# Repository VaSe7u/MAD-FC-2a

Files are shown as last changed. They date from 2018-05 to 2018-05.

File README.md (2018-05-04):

**MAD-FC-2a** quadrocopter flight controller.

This is a project of a flight controller for quadcopter. The [main source file][cpp] is designed to be descriptive of a multirotor flight controller algorithm. It is a concrete implementation that uses ATmega328P, MPU9255 and nRF24L01+ hardware but they can be easily replaced. The schematic and board layout for the flight controller and the remote board can be found in their respective circuit folders. The project depends on [MAD][madLink] library which is a common library for the flight controller and the remote.

*Not tested, Old project: [FC-alpha2][fcAlpha2].*

Flight Controller
=================
Schematic:
----------
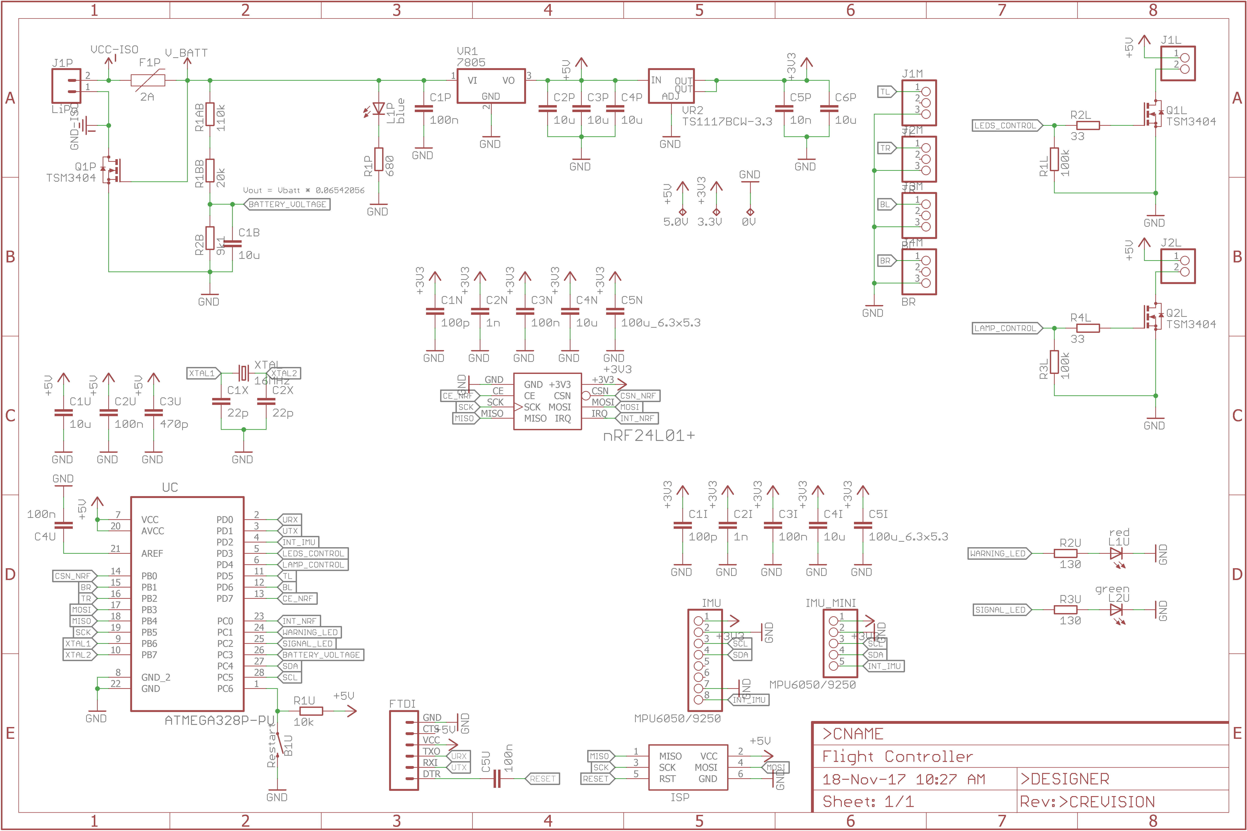
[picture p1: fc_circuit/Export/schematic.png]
sch


Board:
----------
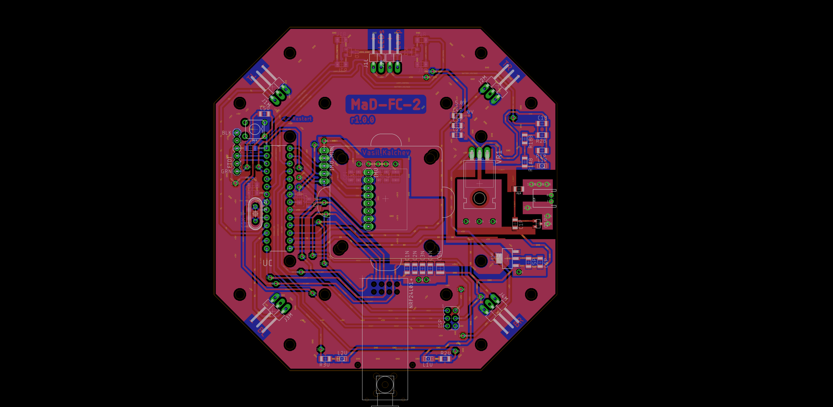
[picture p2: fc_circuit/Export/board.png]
brd

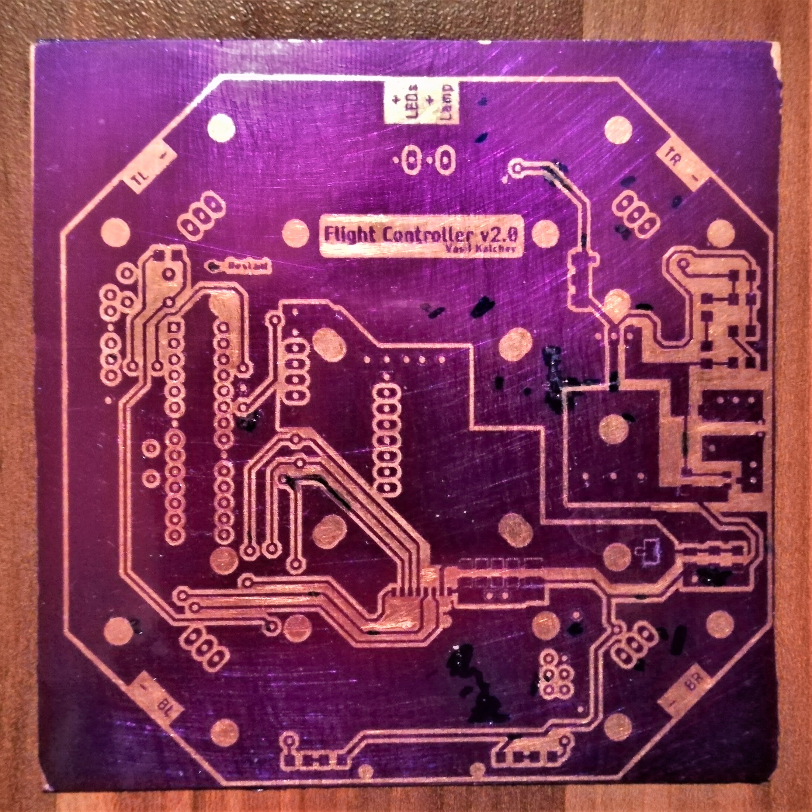
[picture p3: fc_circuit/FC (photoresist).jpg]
brdPhoto1

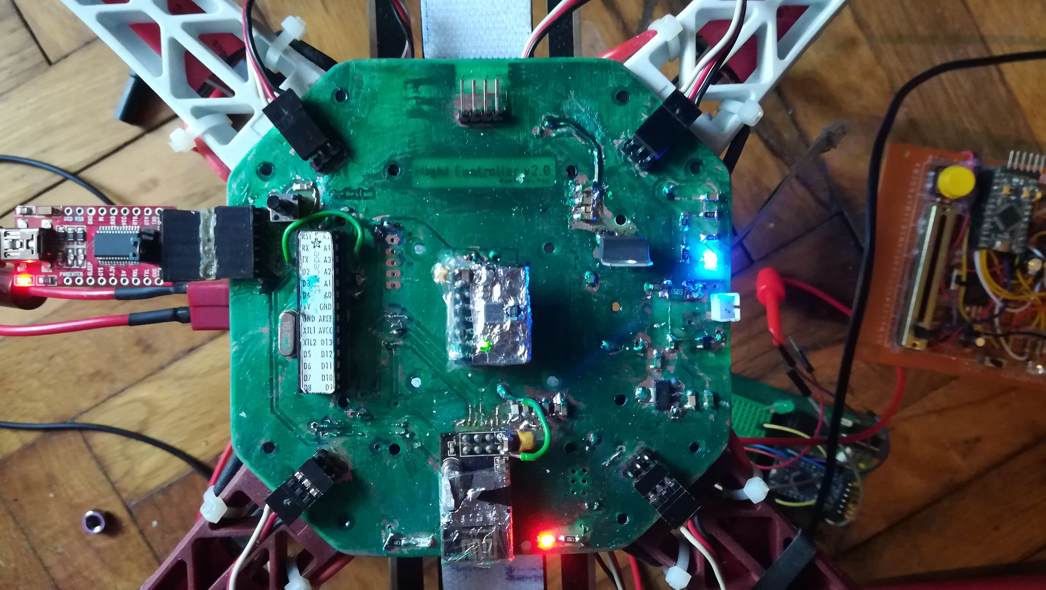
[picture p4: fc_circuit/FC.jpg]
brdPhoto2


Photo:
----------
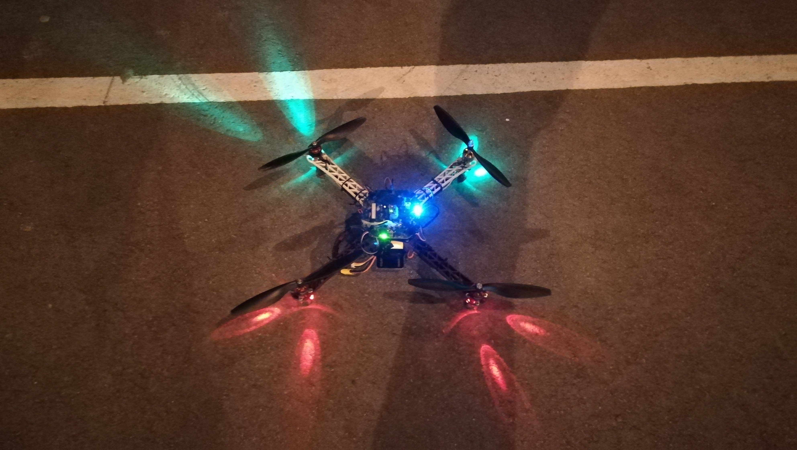
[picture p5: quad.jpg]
quadPhoto


Remote
======
Schematic:
----------
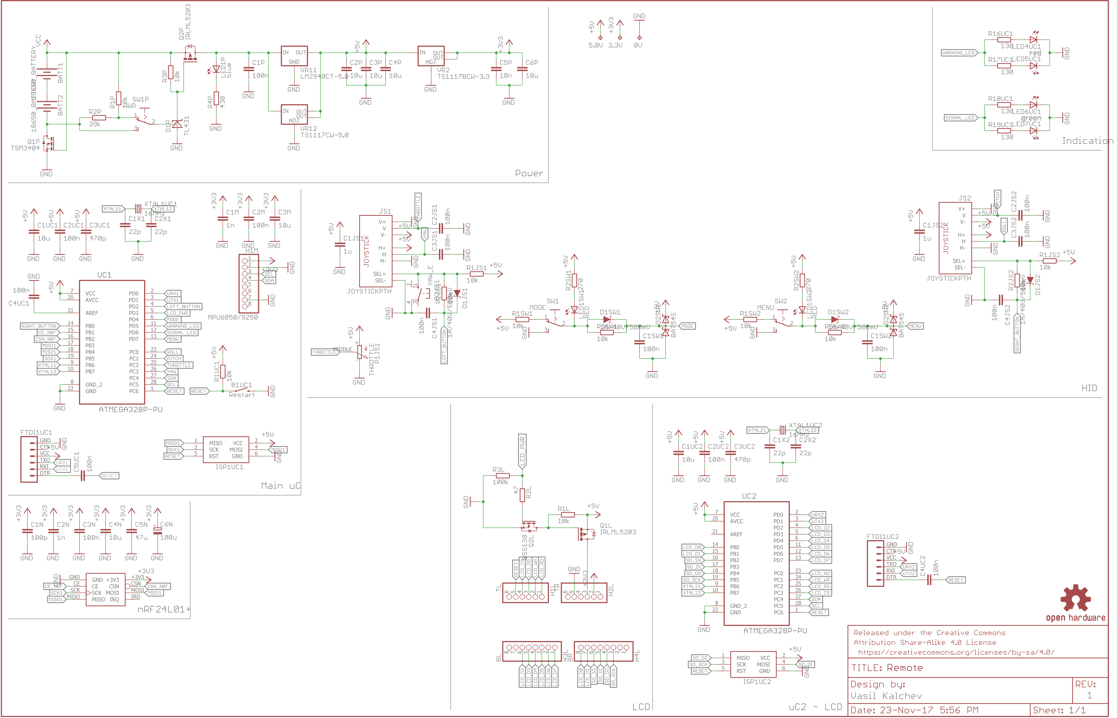
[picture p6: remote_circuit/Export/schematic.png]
rsch


Board:
----------
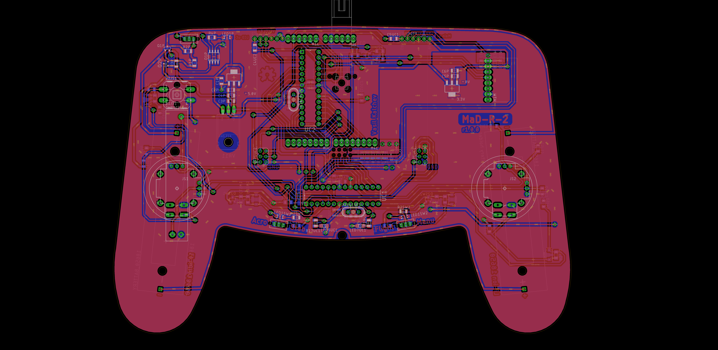
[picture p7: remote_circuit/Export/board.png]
rbrd


License
=======
The MIT License (MIT)

Copyright (c) 2016 Vasil Kalchev

Permission is hereby granted, free of charge, to any person obtaining a copy
of this software and associated documentation files (the "Software"), to deal
in the Software without restriction, including without limitation the rights
to use, copy, modify, merge, publish, distribute, sublicense, and/or sell
copies of the Software, and to permit persons to whom the Software is
furnished to do so, subject to the following conditions:

The above copyright notice and this permission notice shall be included in all
copies or substantial portions of the Software.

THE SOFTWARE IS PROVIDED "AS IS", WITHOUT WARRANTY OF ANY KIND, EXPRESS OR
IMPLIED, INCLUDING BUT NOT LIMITED TO THE WARRANTIES OF MERCHANTABILITY,
FITNESS FOR A PARTICULAR PURPOSE AND NONINFRINGEMENT. IN NO EVENT SHALL THE
AUTHORS OR COPYRIGHT HOLDERS BE LIABLE FOR ANY CLAIM, DAMAGES OR OTHER
LIABILITY, WHETHER IN AN ACTION OF CONTRACT, TORT OR OTHERWISE, ARISING FROM,
OUT OF OR IN CONNECTION WITH THE SOFTWARE OR THE USE OR OTHER DEALINGS IN THE
SOFTWARE.

[cpp]: https://github.com/VaSe7u/MAD-FC-2a/blob/master/code/MAD-FC-2a.ino
[madLink]: https://github.com/VaSe7u/MAD
[fcAlpha2]: https://github.com/VaSe7u/FC-alpha2

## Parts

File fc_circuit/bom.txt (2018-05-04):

Qty Value         Device                          Package
2   33            Resistor                        1206
2   130           Resistor                        1206
1   680           Resistor                        1206
1   9k1           Resistor                        1206
1   20k           Resistor                        1206
1   10k           Resistor                        1206
2   100k          Resistor                        1206
1   110k          Resistor                        1206

2   22p           Ceramic capacitor               1206
2   100p          Ceramic capacitor               1206
1   470p          Ceramic capacitor               1206
2   1n            Ceramic capacitor               1206
1   10n           Ceramic capacitor               1206
6   100n          Ceramic capacitor               1206
8   10u           Ceramic capacitor               1206

1   Conn          CONN_02JST-PTH-2                JST-2-PTH

1   SWITCH        MOMENTARY-SWITCH-SPST-PTH-6.0MM 6.0mm

1   blue          LED                             1206
1   green         LED                             1206
1   red           LED                             1206

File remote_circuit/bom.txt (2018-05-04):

Qty Value             Device                              Package
1   47                Resistor                            1206
4   130               Resistor                            1206
2   270               Resistor                            1206
1   430               Resistor                            1206
12  10k               Resistor                            1206
1   39k               Resistor                            1206
1   100k              Resistor                            1206

4   22p               Ceramic capacitor 16V               1206
1   100p              Ceramic capacitor 16V               1206
2   470p              Ceramic capacitor 16V               1206
2   1n                Ceramic capacitor 16V               1206
1   10n               Ceramic capacitor 16V               1206
16  100n              Ceramic capacitor 16V               1206
2   1u                Ceramic capacitor 16V               1206
8   10u               Ceramic capacitor 16V               1206
1   100u              Electrolytic capacitor 16V          6.3x5.3

1   TL431             TL431                               SO-8

1   BSS138            Transistor                          SOT23
2   IRLML5203         Transistor                          MICRO3

1   LM2940CT-5.0      Voltage regulator                   TO-220
1   TS1117CW-5.0      Voltage regulator                   SOT223
1   TS1117BCW-3.3     Voltage regulator                   SOT223

1   MOMENTARY-SWITCH  MOMENTARY-SWITCH-SPST-SMD           6x3,8mm

1   blue              LED                                 1206
2   green             LED                                 1206
4   red               LED                                 1206

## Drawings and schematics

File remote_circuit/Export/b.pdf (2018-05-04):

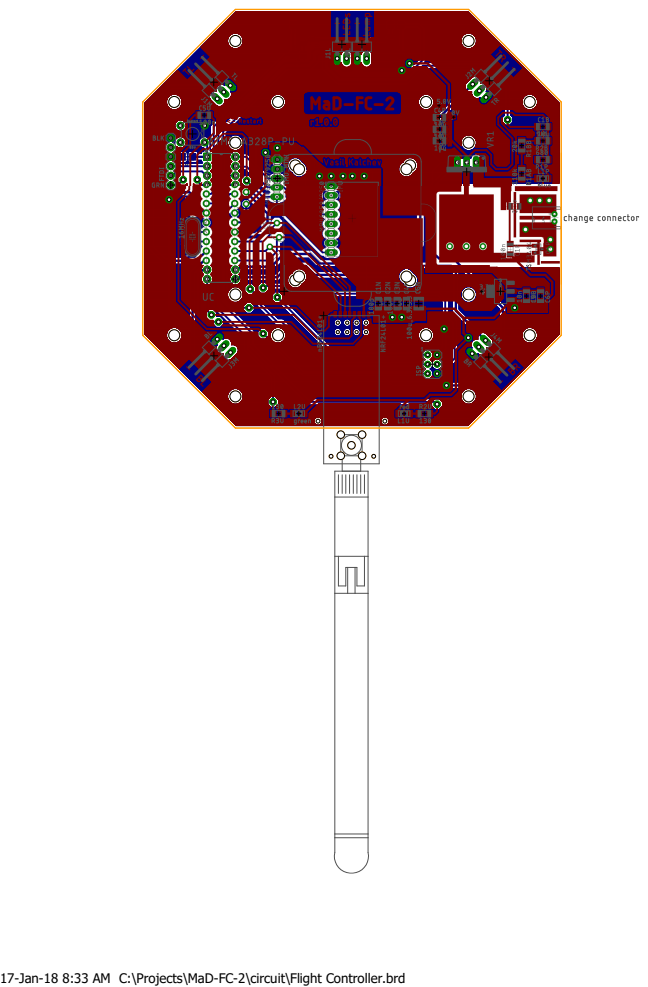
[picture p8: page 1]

17-Jan-18 8:33 AM C:\Projects\MaD-FC-2\circuit\Flight Controller.brd

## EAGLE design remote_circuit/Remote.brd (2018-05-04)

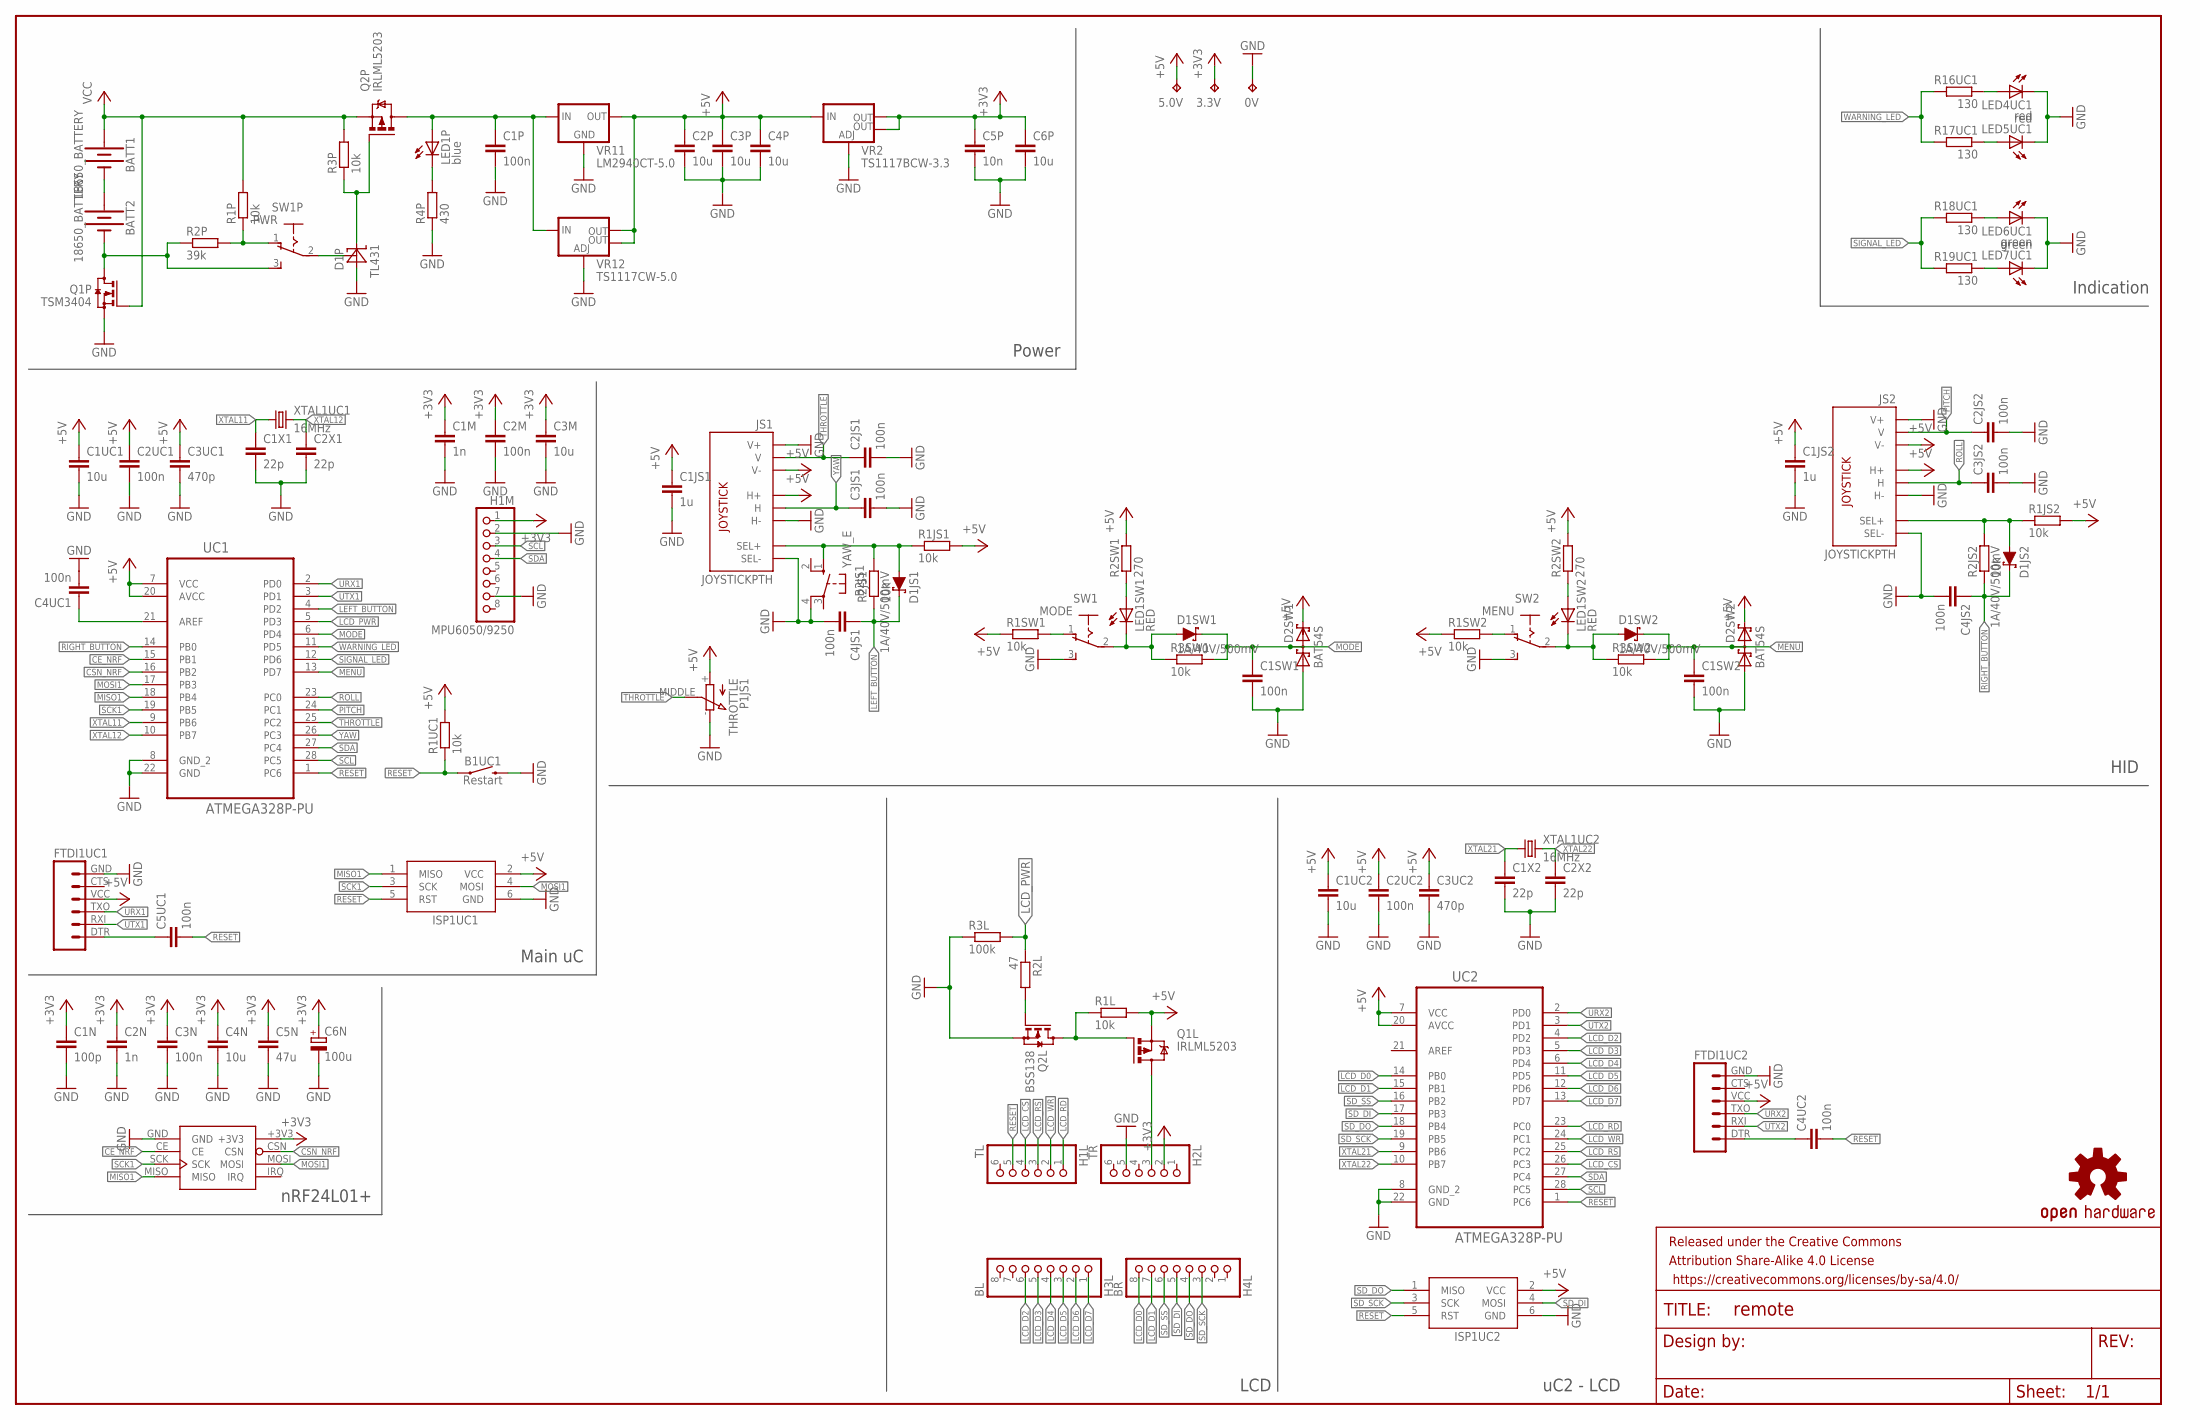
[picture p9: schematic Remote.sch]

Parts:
0V, 3.3V, 5.0V: TPTP10SQ; TP10SQ
B1: nRF24L01+; NRF24L01+_PA_LNA
B1UC1: Restart; TACTILE_SWITCH_SMD_6.0X3.5MM
B2JS1: YAW_E; B3F-40XX
BATT1, BATT2: 18650_BATTERY; BATTERY_HOLDER_18650
C1JS1, C1JS2: 1u; C1206
C1M, C2N: 1n; C1206
C1N: 100p; C1206
C1P, C1SW1, C1SW2, C2JS1, C2JS2, C2M, C2UC1, C2UC2, C3JS1, C3JS2, C3N, C4JS1, C4JS2, C4UC1, C4UC2, C5UC1: 100n; C1206
C1UC1, C1UC2, C2P, C3M, C3P, C4N, C4P, C6P: 10u; C1206
C1X1, C1X2, C2X1, C2X2: 22p; C1206
C3UC1, C3UC2: 470p; C1206
C5N: 47u; C3225
C5P: 10n; C1206
C6N: 100u; 153CLV-0505
D1JS1, D1JS2, D1SW1, D1SW2: 1A/40V/500mV; SMA-DIODE
D1P: TL431; SO-8
D2SW1, D2SW2: BAT54S; SOT23
FRAME2: FRAME-LEDGER; CREATIVE_COMMONS
FTDI1UC1, FTDI1UC2: FTDI_BASICPTH; FTDI_BASIC
H1L: TL; 1X06
H1M: MPU6050/9250; 1X08
H2L: TR; 1X06
H3L: BL; 1X08
H4L: BR; 1X08
ISP1UC1, ISP1UC2: AVRISP-6; AVRISP
JS1, JS2: JOYSTICKPTH; JOYSTICK
LED1P: blue; SML1206
LED1SW1, LED1SW2: RED; SML1206
LED4UC1: red; SML1206
LED5UC1: red; 1206
LED6UC1: green; SML1206
LED7UC1: green; 1206
LOGO1: OSHW-LOGOL-COPPER; OSHW-LOGO-L_COPPER
P1JS1: THROTTLE; SLIDE_POTENTIOMETER
Q1L, Q2P: IRLML5203; MICRO3
Q1P: TSM3404; SOT23
Q2L: BSS138; SOT23
R1JS1, R1JS2, R1L, R1P, R1SW1, R1SW2, R1UC1, R2JS1, R2JS2, R3P, R3SW1, R3SW2: 10k; R1206
R2L: 47; R1206
R2P: 39k; R1206
R2SW1, R2SW2: 270; R1206
R3L: 100k; R1206
R4P: 430; R1206
R16UC1, R17UC1, R18UC1, R19UC1: 130; R1206
SW1: MODE; SWITCH_2MM
SW1P: PWR; SWITCH_2MM
SW2: MENU; SWITCH_2MM
UC1, UC2: ATMEGA328P-PU; DIP254P762X457-28
VR2: TS1117BCW-3.3; SOT223
VR11: LM2940CT-5.0; 78XXL
VR12: TS1117CW-5.0; SOT223
XTAL1UC1, XTAL1UC2: 16MHz; HC49/S

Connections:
+3V3: 3.3V.TP, B1.+3V3, C1M.1, C1N.1, C2M.1, C2N.1, C3M.1, C3N.1, C4N.1, C5N.1, C5P.1, C6N.+, C6P.1, H1M.1, H2L.2, VR2.2 (OUT), VR2.4 (OUT)
+5V: 5.0V.TP, C1JS1.1, C1JS2.1, C1UC1.1, C1UC2.1, C2P.1, C2UC1.1, C2UC2.1, C3P.1, C3UC1.1, C3UC2.1, C4P.1, D2SW1.2 (C2), D2SW2.2 (C2), FTDI1UC1.VCC (4), FTDI1UC2.VCC (4), ISP1UC1.2 (VCC), ISP1UC2.2 (VCC), JS1.H1 (H+), JS1.V3 (V-), JS2.H1 (H+), JS2.V3 (V-), P1JS1.+, Q1L.2 (S), R1JS1.2, R1JS2.2, R1L.2, R1SW1.1, R1SW2.1, R1UC1.2, R2SW1.2, R2SW2.2, UC1.7 (VCC), UC1.20 (AVCC), UC2.7 (VCC), UC2.20 (AVCC), VR2.3 (IN), VR11.OUT, VR12.2 (OUT), VR12.4 (OUT)
CE_NRF: B1.CE, UC1.15 (PB1)
CSN_NRF: B1.CSN, UC1.16 (PB2)
GND: 0V.TP, B1.GND, B1UC1.2, B2JS1.4 (P1), C1JS1.2, C1JS2.2, C1M.2, C1N.2, C1P.2, C1SW1.2, C1SW2.2, C1UC1.2, C1UC2.2, C1X1.2, C1X2.2, C2JS1.2, C2JS2.2, C2M.2, C2N.2, C2P.2, C2UC1.2, C2UC2.2, C2X1.2, C2X2.2, C3JS1.2, C3JS2.2, C3M.2, C3N.2, C3P.2, C3UC1.2, C3UC2.2, C4JS1.2, C4JS2.2, C4N.2, C4P.2, C4UC1.2, C5N.2, C5P.2, C6N.-, C6P.2, D1P.2 (ANODE), D1P.3 (ANODE), D1P.6 (ANODE), D1P.7 (ANODE), D2SW1.1 (A1), D2SW2.1 (A1), FTDI1UC1.GND (6), FTDI1UC2.GND (6), H1M.2, H1M.7, H2L.5, ISP1UC1.6 (GND), ISP1UC2.6 (GND), JS1.B2A (SEL-), JS1.H3 (H-), JS1.V1 (V+), JS2.B2A (SEL-), JS2.H3 (H-), JS2.V1 (V+), LED4UC1.C, LED5UC1.C, LED6UC1.C, LED7UC1.C, P1JS1.-, Q1P.2 (S), Q2L.2 (S), R3L.1, R4P.1, SW1.3, SW2.3, UC1.8 (GND_2), UC1.22 (GND), UC2.8 (GND_2), UC2.22 (GND), VR2.1 (ADJ), VR11.GND, VR12.1 (ADJ)
LCD_CS: H1L.4, UC2.26 (PC3)
LCD_D0: H4L.8, UC2.14 (PB0)
LCD_D1: H4L.7, UC2.15 (PB1)
LCD_D2: H3L.6, UC2.4 (PD2)
LCD_D3: H3L.5, UC2.5 (PD3)
LCD_D4: H3L.4, UC2.6 (PD4)
LCD_D5: H3L.3, UC2.11 (PD5)
LCD_D6: H3L.2, UC2.12 (PD6)
LCD_D7: H3L.1, UC2.13 (PD7)
LCD_PWR: R2L.1, R3L.2, UC1.5 (PD3)
LCD_RD: H1L.1, UC2.23 (PC0)
LCD_RS: H1L.3, UC2.25 (PC2)
LCD_WR: H1L.2, UC2.24 (PC1)
LEFT_BUTTON: C4JS1.1, D1JS1.C, R2JS1.1, UC1.4 (PD2)
MENU: C1SW2.1, D1SW2.C, D2SW2.3 (C1A2), R3SW2.2, UC1.13 (PD7)
MISO1: B1.MISO, ISP1UC1.1 (MISO), UC1.18 (PB4)
MODE: C1SW1.1, D1SW1.C, D2SW1.3 (C1A2), R3SW1.2, UC1.6 (PD4)
MOSI1: B1.MOSI, ISP1UC1.4 (MOSI), UC1.17 (PB3)
unnamed: C4UC1.1, UC1.21 (AREF)
unnamed: LED1SW1.A, R2SW1.1
unnamed: C5UC1.1, FTDI1UC1.DTR (1)
unnamed: BATT1.-, BATT2.+
unnamed: R1SW2.2, SW2.1
unnamed: D1SW2.A, LED1SW2.C, R3SW2.1, SW2.2
unnamed: LED1P.C, R4P.2
unnamed: D1SW1.A, LED1SW1.C, R3SW1.1, SW1.2
unnamed: LED1SW2.A, R2SW2.1
unnamed: R1SW1.2, SW1.1
unnamed: D1JS2.A, JS2.B1A (SEL+), R1JS2.1, R2JS2.2
unnamed: BATT2.-, Q1P.3 (D), R2P.1, SW1P.3
unnamed: LED4UC1.A, R16UC1.1
unnamed: LED6UC1.A, R18UC1.1
unnamed: C4UC2.1, FTDI1UC2.DTR (1)
unnamed: LED5UC1.A, R17UC1.1
unnamed: H2L.3, Q1L.3 (D)
unnamed: LED7UC1.A, R19UC1.1
unnamed: C1P.1, LED1P.A, Q2P.3 (D), VR11.IN, VR12.3 (IN)
unnamed: D1P.8 (REFERENCE), SW1P.2
unnamed: R1P.1, R2P.2, SW1P.1
unnamed: Q1L.1 (G), Q2L.3 (D), R1L.1
unnamed: D1P.1 (CATHODE), Q2P.1 (G), R3P.1
unnamed: Q2L.1 (G), R2L.2
PITCH: C2JS2.1, JS2.V2 (V), UC1.24 (PC1)
RESET: B1UC1.1, C4UC2.2, C5UC1.2, H1L.5, ISP1UC1.5 (RST), ISP1UC2.5 (RST), R1UC1.1, UC1.1 (PC6), UC2.1 (PC6)
RIGHT_BUTTON: C4JS2.1, D1JS2.C, R2JS2.1, UC1.14 (PB0)
ROLL: C3JS2.1, JS2.H2 (H), UC1.23 (PC0)
SCK1: B1.SCK, ISP1UC1.3 (SCK), UC1.19 (PB5)
SCL: H1M.3, UC1.28 (PC5), UC2.28 (PC5)
SDA: H1M.4, UC1.27 (PC4), UC2.27 (PC4)
SD_DI: H4L.5, ISP1UC2.4 (MOSI), UC2.17 (PB3)
SD_DO: H4L.4, ISP1UC2.1 (MISO), UC2.18 (PB4)
SD_SCK: H4L.3, ISP1UC2.3 (SCK), UC2.19 (PB5)
SD_SS: H4L.6, UC2.16 (PB2)
SIGNAL_LED: R18UC1.2, R19UC1.2, UC1.12 (PD6)
SN1: B2JS1.1 (S), D1JS1.A, JS1.B1A (SEL+), R1JS1.1, R2JS1.2
THROTTLE: C2JS1.1, JS1.V2 (V), P1JS1.MIDDLE, UC1.25 (PC2)
URX1: FTDI1UC1.TXO (3), UC1.2 (PD0)
URX2: FTDI1UC2.TXO (3), UC2.2 (PD0)
UTX1: FTDI1UC1.RXI (2), UC1.3 (PD1)
UTX2: FTDI1UC2.RXI (2), UC2.3 (PD1)
VCC: BATT1.+, Q1P.1 (G), Q2P.2 (S), R1P.2, R3P.2
WARNING_LED: R16UC1.2, R17UC1.2, UC1.11 (PD5)
XTAL11: C1X1.1, UC1.9 (PB6), XTAL1UC1.1
XTAL12: C2X1.1, UC1.10 (PB7), XTAL1UC1.2
XTAL21: C1X2.1, UC2.9 (PB6), XTAL1UC2.1
XTAL22: C2X2.1, UC2.10 (PB7), XTAL1UC2.2
YAW: C3JS1.1, JS1.H2 (H), UC1.26 (PC3)

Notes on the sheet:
Power
nRF24L01+
LCD
uC2 - LCD
HID
Indication
Main uC

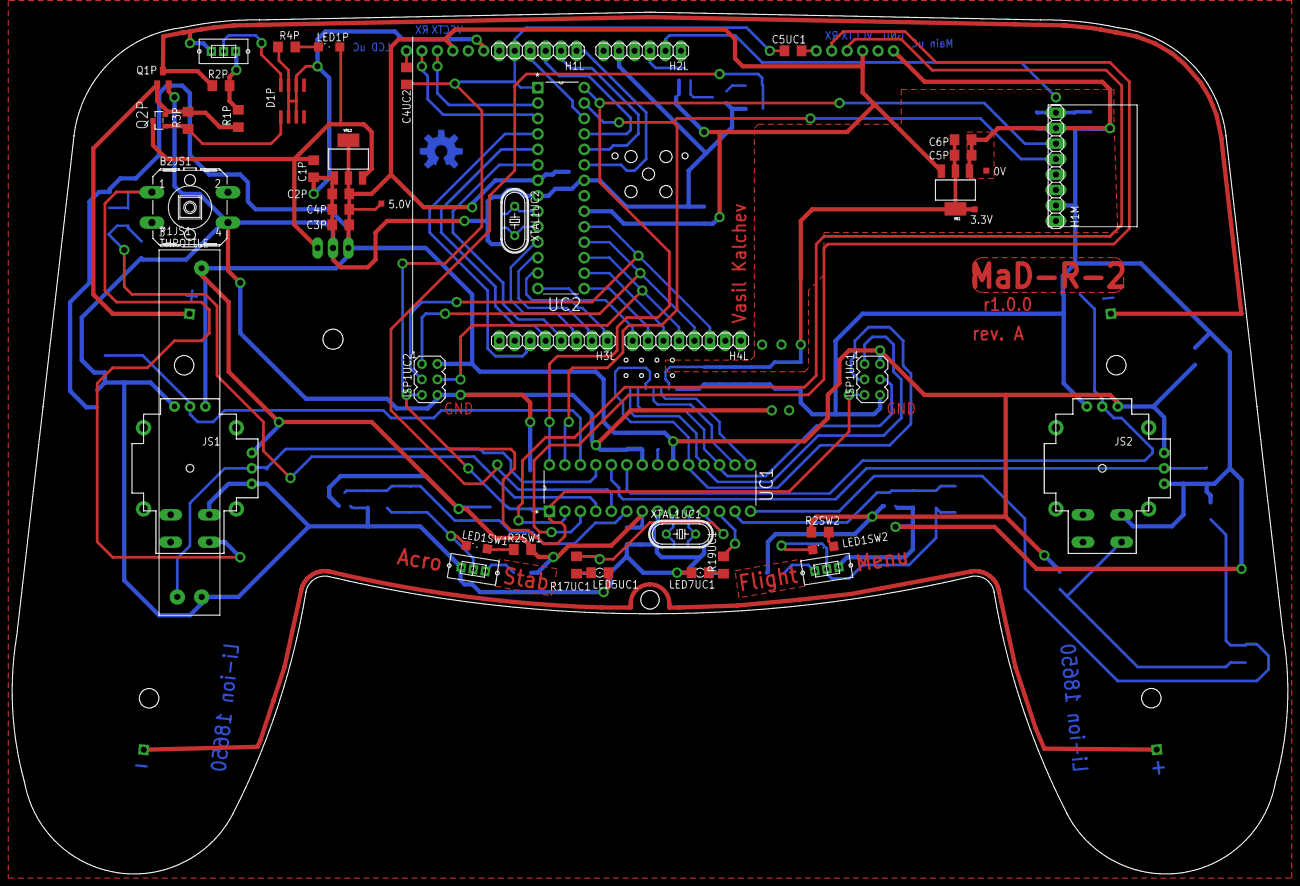
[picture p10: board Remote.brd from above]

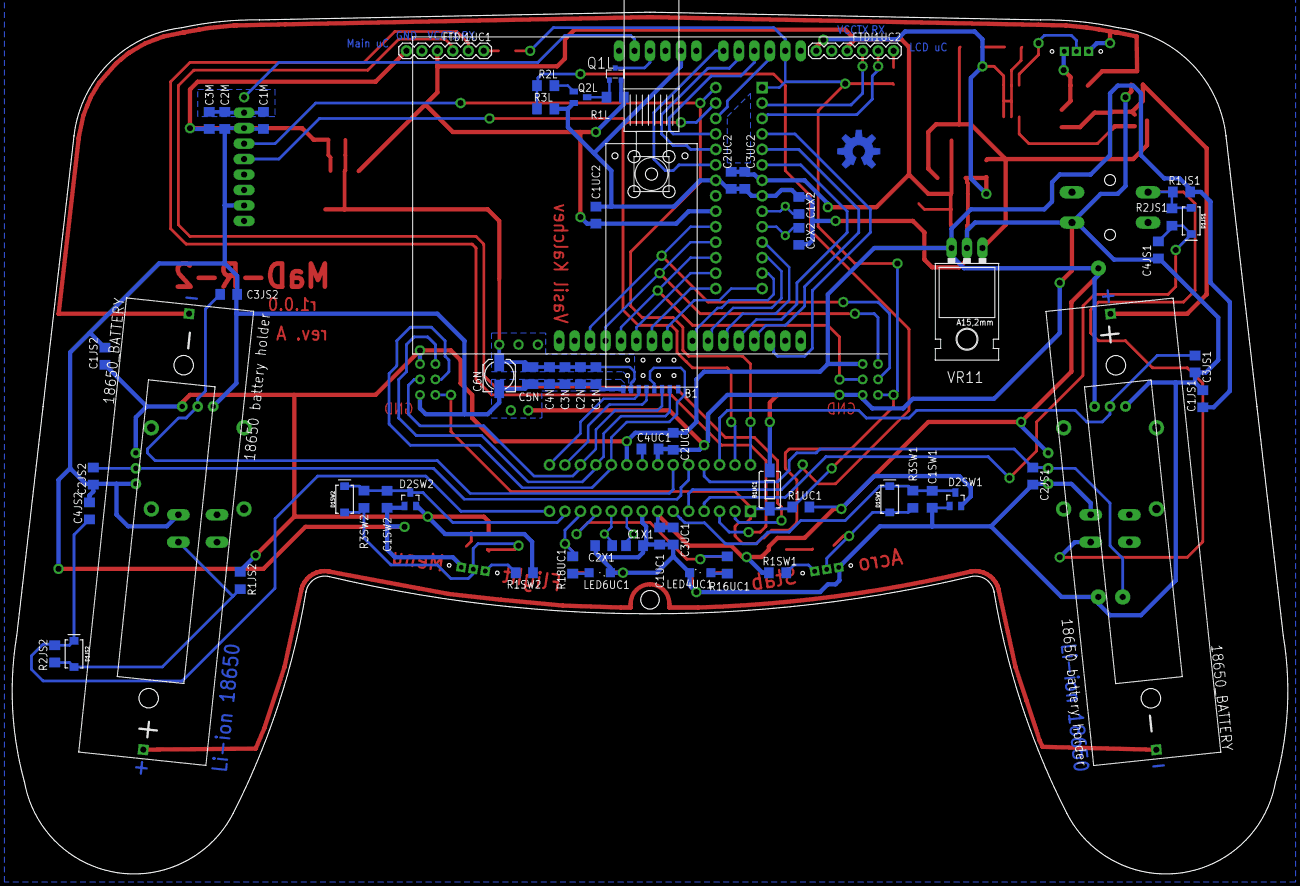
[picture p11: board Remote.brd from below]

Board: 2 copper layers, 209.5 x 141.5 mm, 110 parts (62 on the bottom side), 72 nets.

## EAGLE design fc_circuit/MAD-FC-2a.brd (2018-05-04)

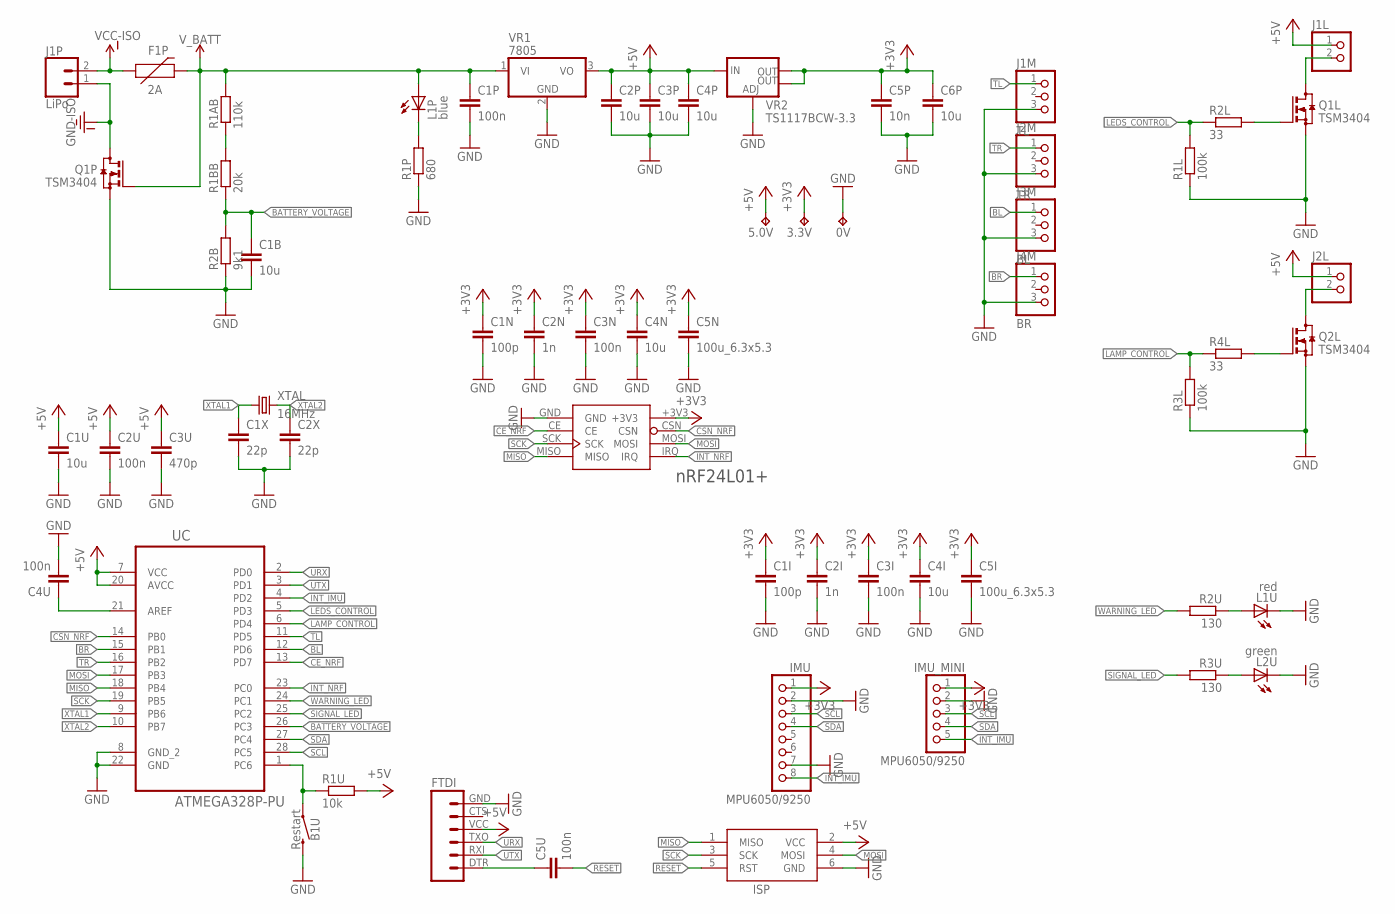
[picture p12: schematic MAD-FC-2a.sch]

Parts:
0V, 3.3V, 5.0V: TPTP10SQ; TP10SQ
B1U: Restart; TACTILE_SWITCH_PTH_6.0MM
C1B, C1U, C2P, C3P, C4I, C4N, C4P, C6P: 10u; C1206
C1I, C1N: 100p; C1206
C1P, C2U, C3I, C3N, C4U, C5U: 100n; C1206
C1X, C2X: 22p; C1206
C2I, C2N: 1n; C1206
C3U: 470p; C1206
C5I, C5N: 100u_6.3x5.3; C3225
C5P: 10n; C1206
F1P: 2A; 1206
FTDI: FTDI_BASICPTH; FTDI_BASIC
IMU: MPU6050/9250; 1X08
IMU_MINI: MPU6050/9250; 1X05
ISP: AVRISP-6; AVRISP
J1L, J2L: PINHD-1X2/90; 1X02/90
J1M: TL; 1X03/90
J1P: LiPo; JST-2-PTH
J2M: TR; 1X03/90
J3M: BL; 1X03/90
J4M: BR; 1X03/90
L1P: blue; 1206
L1U: red; 1206
L2U: green; 1206
NRF24L01+: nRF24L01+; NRF24L01+_PA_LNA_SMD
Q1L, Q1P, Q2L: TSM3404; SOT23
R1AB: 110k; R1206
R1BB: 20k; R1206
R1L, R3L: 100k; R1206
R1P: 680; R1206
R1U: 10k; R1206
R2B: 9k1; R1206
R2L, R4L: 33; R1206
R2U, R3U: 130; R1206
UC: ATMEGA328P-PU; DIP254P762X457-28
VR1: 7805; TO220V
VR2: TS1117BCW-3.3; SOT223
XTAL: 16MHz; HC49/S

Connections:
+3V3: 3.3V.TP, C1I.1, C1N.1, C2I.1, C2N.1, C3I.1, C3N.1, C4I.1, C4N.1, C5I.1, C5N.1, C5P.1, C6P.1, IMU.1, IMU_MINI.1, NRF24L01+.+3V3, VR2.2 (OUT), VR2.4 (OUT)
+5V: 5.0V.TP, C1U.1, C2P.1, C2U.1, C3P.1, C3U.1, C4P.1, FTDI.VCC (4), ISP.2 (VCC), J1L.1, J2L.1, R1U.2, UC.7 (VCC), UC.20 (AVCC), VR1.3 (VO), VR2.3 (IN)
BATTERY_VOLTAGE: C1B.1, R1BB.1, R2B.2, UC.26 (PC3)
BL: J3M.1, UC.12 (PD6)
BR: J4M.1, UC.15 (PB1)
CE_NRF: NRF24L01+.CE, UC.13 (PD7)
CSN_NRF: NRF24L01+.CSN, UC.14 (PB0)
GND: 0V.TP, B1U.3 (2), C1B.2, C1I.2, C1N.2, C1P.2, C1U.2, C1X.2, C2I.2, C2N.2, C2P.2, C2U.2, C2X.2, C3I.2, C3N.2, C3P.2, C3U.2, C4I.2, C4N.2, C4P.2, C4U.2, C5I.2, C5N.2, C5P.2, C6P.2, FTDI.GND (6), IMU.2, IMU.7, IMU_MINI.2, ISP.6 (GND), J1M.3, J2M.3, J3M.3, J4M.3, L1U.C, L2U.C, NRF24L01+.GND, Q1L.2 (S), Q1P.2 (S), Q2L.2 (S), R1L.1, R1P.1, R2B.1, R3L.1, UC.8 (GND_2), UC.22 (GND), VR1.2 (GND), VR2.1 (ADJ)
GND-ISO: J1P.1, Q1P.3 (D)
INT_IMU: IMU.8, IMU_MINI.5, UC.4 (PD2)
INT_NRF: NRF24L01+.IRQ, UC.23 (PC0)
LAMP_CONTROL: R3L.2, R4L.1, UC.6 (PD4)
LAMP_SINK: J2L.2, Q2L.3 (D)
LEDS_CONTROL: R1L.2, R2L.1, UC.5 (PD3)
LEDS_SINK: J1L.2, Q1L.3 (D)
MISO: ISP.1 (MISO), NRF24L01+.MISO, UC.18 (PB4)
MOSI: ISP.4 (MOSI), NRF24L01+.MOSI, UC.17 (PB3)
unnamed: L2U.A, R3U.1
unnamed: R1AB.1, R1BB.2
unnamed: L1U.A, R2U.1
unnamed: Q1L.1 (G), R2L.2
unnamed: Q2L.1 (G), R4L.2
unnamed: L1P.C, R1P.2
unnamed: C4U.1, UC.21 (AREF)
unnamed: C5U.1, FTDI.DTR (1)
RESET: B1U.1, C5U.2, ISP.5 (RST), R1U.1, UC.1 (PC6)
SCK: ISP.3 (SCK), NRF24L01+.SCK, UC.19 (PB5)
SCL: IMU.3, IMU_MINI.3, UC.28 (PC5)
SDA: IMU.4, IMU_MINI.4, UC.27 (PC4)
SIGNAL_LED: R3U.2, UC.25 (PC2)
TL: J1M.1, UC.11 (PD5)
TR: J2M.1, UC.16 (PB2)
URX: FTDI.TXO (3), UC.2 (PD0)
UTX: FTDI.RXI (2), UC.3 (PD1)
VCC-ISO: F1P.1, J1P.2
V_BATT: C1P.1, F1P.2, L1P.A, Q1P.1 (G), R1AB.2, VR1.1 (VI)
WARNING_LED: R2U.2, UC.24 (PC1)
XTAL1: C1X.1, UC.9 (PB6), XTAL.1
XTAL2: C2X.1, UC.10 (PB7), XTAL.2

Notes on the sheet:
nRF24L01+

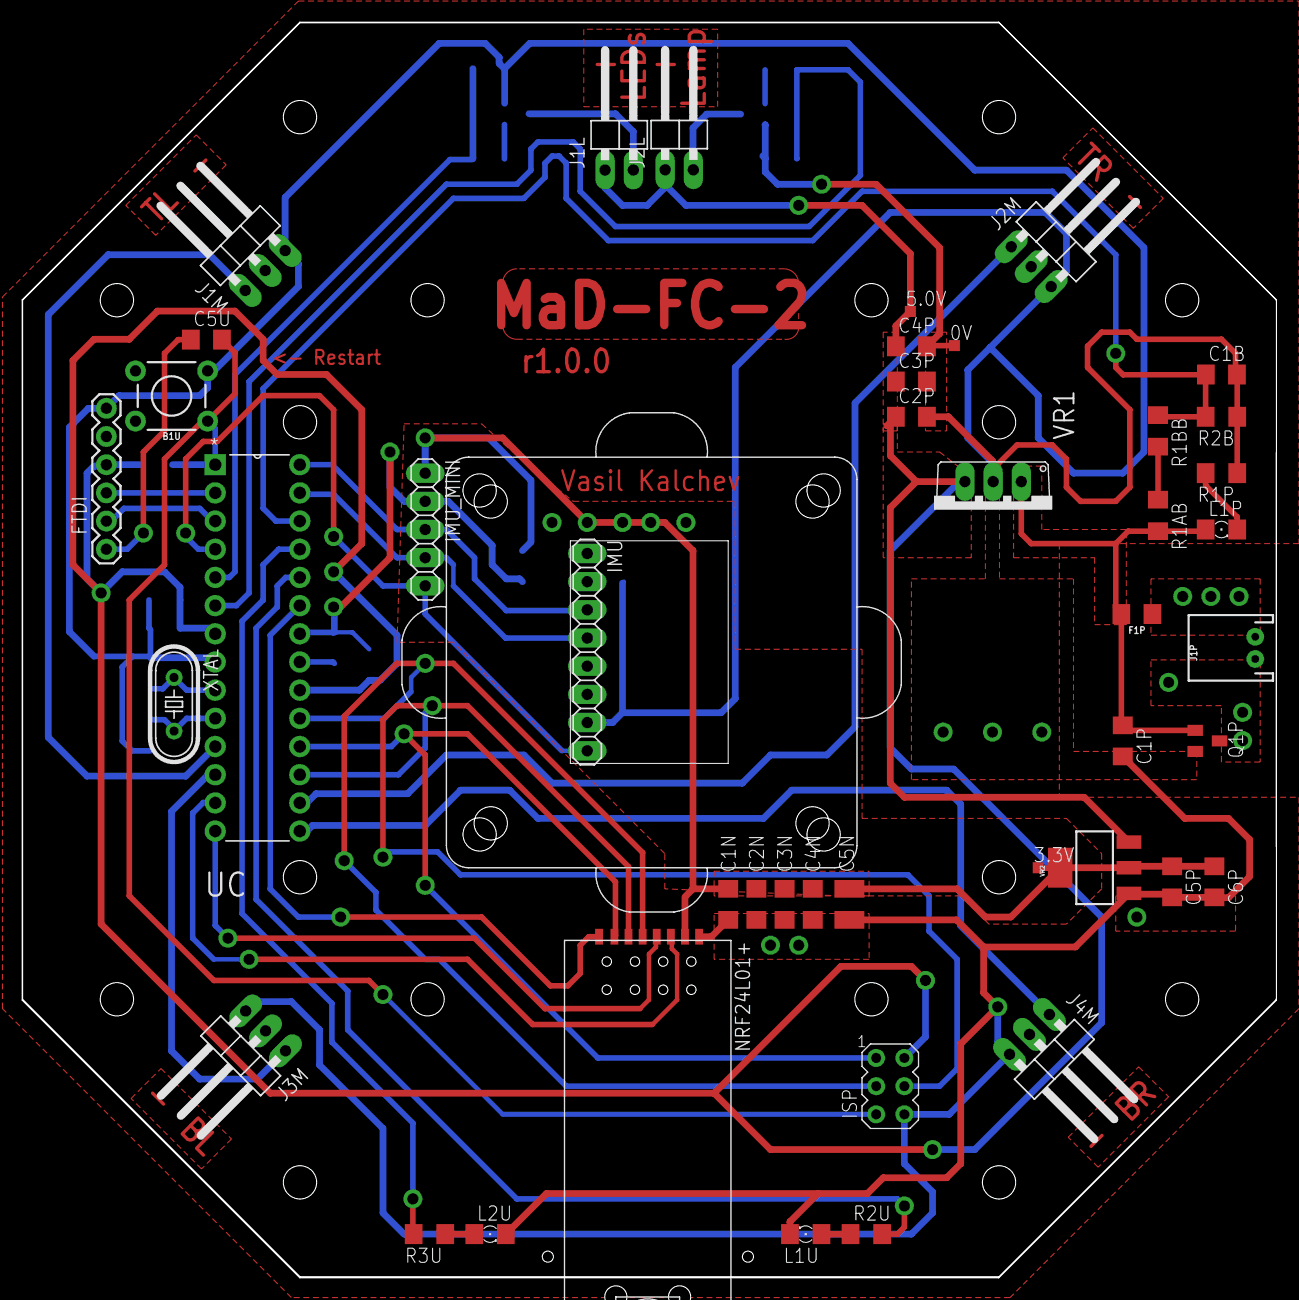
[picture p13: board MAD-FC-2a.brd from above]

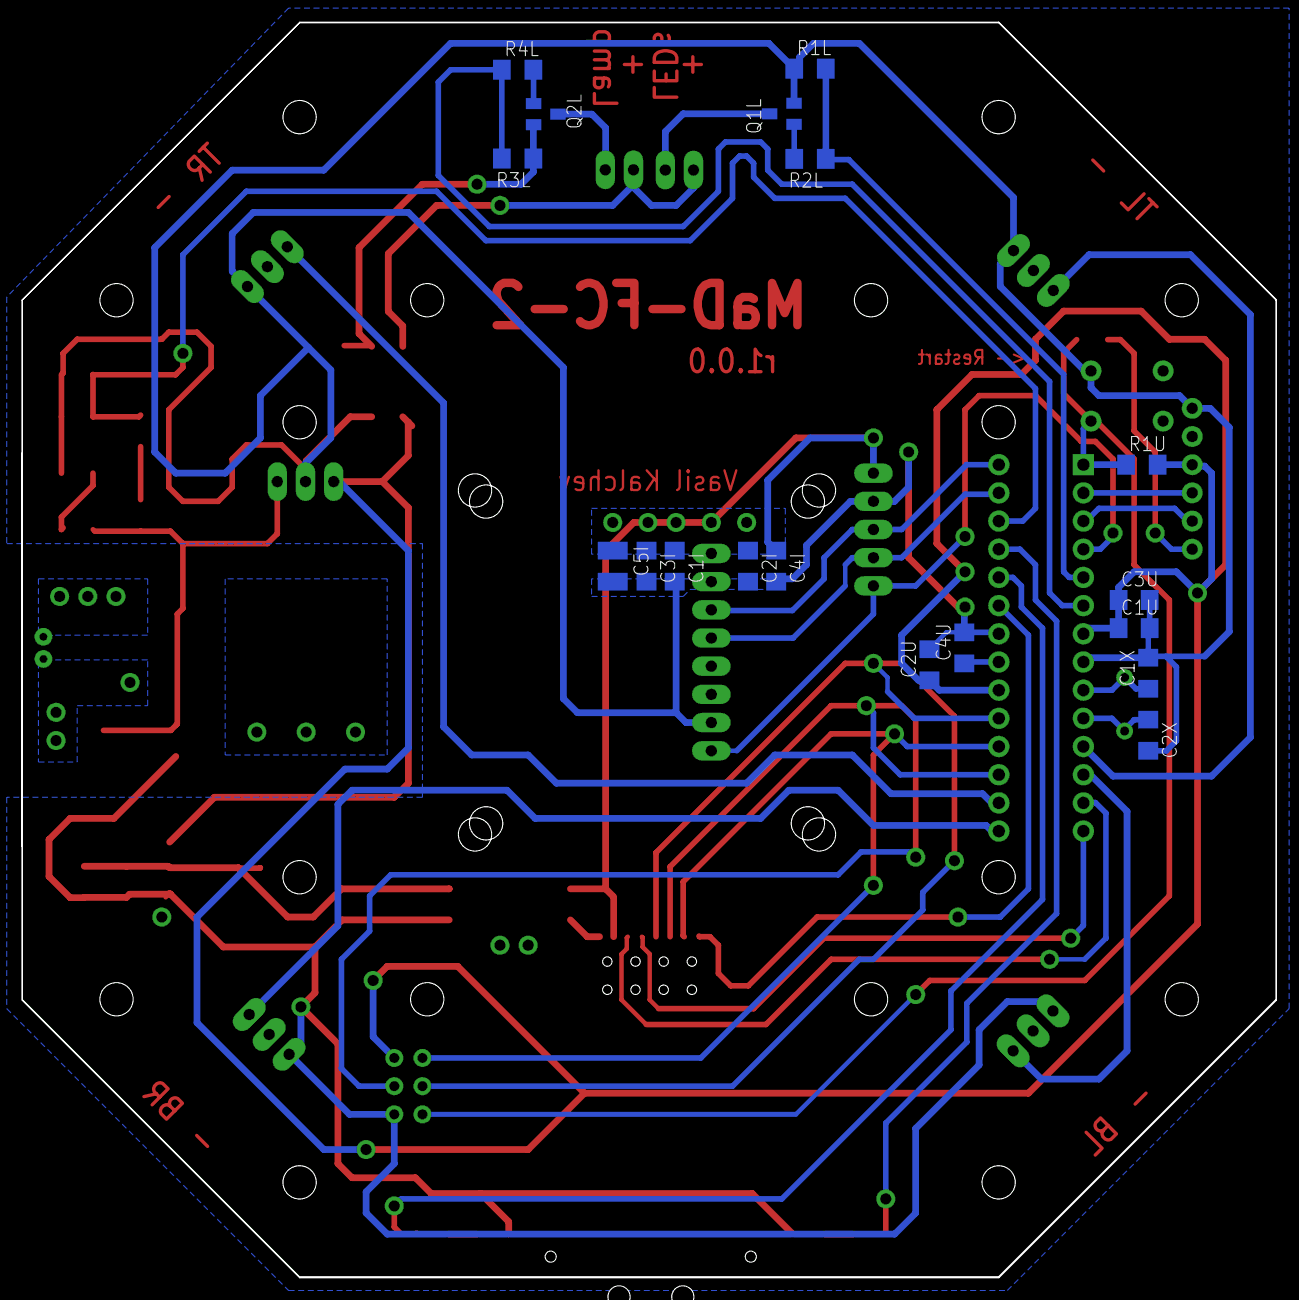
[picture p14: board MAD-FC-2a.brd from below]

Board: 2 copper layers, 113.0 x 113.2 mm, 64 parts (18 on the bottom side), 39 nets.

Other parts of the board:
U$2: F450_TOP_PLATE
U$3: ANTI-VIBRATION_PLATE

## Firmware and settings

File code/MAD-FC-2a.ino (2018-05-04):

// License...

/* TODO:
// turn off if large acceleration and not moving

// Self tests with fake data
// set angular velocity z to positive value - check if motors react
// set control pitch to left - check if motors react
// check if Eaccel == 1g
// check if Eav == 0
// check if Az == 1g
// check if integrating correctly (pids and av yaw)
// check if loop time is constant and under certain value
*/

/* TOC

*/

// Nonvolatile preference increment based on data type

#define F_CPU 16000000


#include "MAD-FC-2a_config.hpp"

/* MAD-FC-2a_debug defines macros 'DEBUG_INITIALIZE(baud)', 'DEBUG(...)'
   and 'DEBUGLN(...)' based on the definition of 'DEBUGGING' in
   MAD-FC-2a_config.hpp. This allows turning on/off UART debugging
   messages from a single place. */
#include "MAD-FC-2a_debug.hpp"

/* MAD-FC-2a_board defines how the microcontroller is connected to board
   "2a" and provides functions for controlling the basic peripherals. */
#include "MAD-FC-2a_board.hpp"

#include <MAD-DataTypes.hpp>
#include <MAD-Utils.hpp>

/* UART_atmega328 library is an alternative to the Arduino's library for
   working with the UART. It is specifically for the ATmega328, it lacks a
   lot of functionality and is meant to be used for simple debugging
   messages while eliminating the requirement of using the Arduino's IDE. */
#include <UART_atmega328.hpp> // https://github.com/VaSe7u/UART_atmega328

/* ADC_atmega328 library is an alternative to the Arduino's functions for
   working with the ADC. It is specifically for the ATmega328 and provides
   functions for setting a trigger source and changing the ADC circuit's
   operating frequency. */
#include <ADC_atmega328.hpp> // https://github.com/VaSe7u/ADC_atmega328

#include <MPU925x_I2C.hpp> // https://github.com/VaSe7u/MPU925x_I2C
#include <AK8963_I2C.hpp> // https://github.com/VaSe7u/AK8963_I2C
#include <i2c_BMP280.h> // https://github.com/orgua/iLib

/* MahonyAHRS is a library implementing Mahony's orientation filter for
   fusing accelerometer, gyroscope and possibly magnetometer.
   This is a fork of https://github.com/PaulStoffregen/MahonyAHRS, the
   main difference is that angular velocity is passed to the filter in
   radians/s. */
#include <MahonyAHRS.h> // https://github.com/VaSe7u/MahonyAHRS

#include <PIDcontroller.hpp> // https://github.com/VaSe7u/PIDcontroller

#include <avr/wdt.h>


/* This function makes sure that the code that follows it, is executed at
   a constant period. It uses the cycle period, which is specified manually
   in MAD-FC-2a_config.hpp based on the longest time it takes for a cycle to
   complete with SYNCHRONIZE turned off and the last time (in microseconds)
   this part of the code was reached. The argument "lastMicroseconds" is
   passed as a reference and is automatically updated. */
void syncCycle(uint32_t& lastMicroseconds) {
# if SYNCHRONIZE
  while (us() - lastMicroseconds < config::cyclePeriod);
  lastMicroseconds = us();
# else
#   warning "SYNCHRONIZE is off!"
  lastMicroseconds = lastMicroseconds;
# endif
}


// Function prototypes.
void updateIndication();
float readBattery();
void updateTelemetryMessage();
void adjustControllers();
void updateTelemetryMessage();
bool commandHandler();
bool settingHandler();


int main() {
  wdt_disable();

  // MAD-FC-2a-board.hpp
  board::initializeTimers();
  /* Configures timer 0 and 1 for 490Hz Fast PWM for the motors
     and timer 2 for counting the microseconds since boot. */
  board::initIO(); // Configures the pins for input or output.

  board::indication::signal(false);
  board::indication::warning(true);
  board::indication::arms(0);
  board::indication::lamp(false);
  // Only red LED is lit while initializing.


  DEBUG_INITIALIZE(config::debug::baud);
  DEBUG("MAD-FC-2a\n=========\n\n");


  // Global objects.
  // ===============
  adc::initialize(adc::Reference::INTERNAL1V1); // link to API
  adc::setAutoTriggerSource(adc::AutoTriggerSource::FreeRunningMode);


  namespace imu {
  MPU925x_I2C mpu; // link to API
  bool init = true;
  mpu.initialize();
  init &= mpu.setAccelFullScaleRange(config::imu::mpu925x::accelerometer::range);
  init &= mpu.setGyroFullScaleRange(config::imu::mpu925x::gyroscope::range);
  init &= mpu.setAccelDLPF(config::imu::mpu925x::accelerometer::dlpf);
  init &= mpu.setGyroDLPF(config::imu::mpu925x::gyroscope::dlpf);
  mpu.setXAccelOffset(board::imu::mpu925x::offset::accelerometer::x());
  mpu.setYAccelOffset(board::imu::mpu925x::offset::accelerometer::y());
  mpu.setZAccelOffset(board::imu::mpu925x::offset::accelerometer::z());
  mpu.setXGyroOffset (board::imu::mpu925x::offset::gyroscope::x());
  mpu.setYGyroOffset (board::imu::mpu925x::offset::gyroscope::y());
  mpu.setZGyroOffset (board::imu::mpu925x::offset::gyroscope::z());
  init &= mpu.testConnection();

  // AK8963_I2C compass;
  } //namespace imu


  namespace altimeter {
  BMP280 bmp;
  bool init = true;
  bmp.initialize();
  bmp.setPressureOversampleRatio(config::altimeter::bmp280::pressureOversampleRatio);
  bmp.setTemperatureOversampleRatio(config::altimeter::bmp280::temperatureOversampleRatio);
  bmp.setFilterRatio(config::altimeter::bmp280::filterRatio);
  bmp.setStandby(config::altimeter::bmp280::standbyTime);
  bmp.setEnabled(true);
  } //namespace altimeter


  namespace fusion {
  Mahony mahony(config::cyclePeriod);
  mahony.setP(config::fusion::mahony::p);
  mahony.setI(config::fusion::mahony::i);
  } //namespace fusion


  namespace controller {
  bool init = true;
  namespace inner {

  const PIDconfig pitchAndRollConfig;
  pitchAndRollConfig.state = true;
  pitchAndRollConfig.p = config::controller::inner::p();
  pitchAndRollConfig.updatePeriod = config::controller::inner::updatePeriod;
  pitchAndRollConfig.minimalOutput = 0 - config::controller::inner::outputRange;
  pitchAndRollConfig.maximalOutput = config::controller::inner::outputRange;

  const PIDconfig yawConfig;
  yawConfig.state = true;
  yawConfig.p = config::controller::inner::yaw::p();
  yawConfig.i = config::controller::inner::yaw::i();
  yawConfig.updatePeriod = config::controller::inner::updatePeriod;
  yawConfig.minimalOutput = 0 - config::controller::inner::outputRange;
  yawConfig.maximalOutput = config::controller::inner::outputRange;
  yawConfig.maximalNegativeIntegralSum = 0 - config::controller::inner::yaw::maximalIntegralSum;
  yawConfig.maximalPositiveIntegralSum = config::controller::inner::yaw::maximalIntegralSum;

  PIDcontroller pitch;
  init &= pitch.config(pitchAndRollConfig);
  PIDcontroller roll;
  init &= roll.config(pitchAndRollConfig);
  PIDcontroller yaw;
  init &= yaw.config(yawConfig);
  } //namespace inner

  namespace outer {

  const PIDconfig pitchAndRollConfig;
  pitchAndRollConfig.state = true;
  pitchAndRollConfig.p = config::controller::outer::p();
  pitchAndRollConfig.i = config::controller::outer::i();
  pitchAndRollConfig.updatePeriod = config::controller::outer::updatePeriod;
  pitchAndRollConfig.minimalOutput = 0 - config::controller::outer::outputRange;
  pitchAndRollConfig.maximalOutput = config::controller::outer::outputRange;
  pitchAndRollConfig.maximalNegativeIntegralSum = 0 - config::controller::outer::maximalIntegralSum;
  pitchAndRollConfig.maximalPositiveIntegralSum = config::controller::outer::maximalIntegralSum;

  PIDcontroller pitch;
  init &= pitch.config(pitchAndRollConfig);
  PIDcontroller roll;
  init &= roll.config(pitchAndRollConfig);
  } //namespace outer
  } //namespace controller


  namespace com {
  RF24 rf24(7, 8); // Arduino pins 7 and 8.
  bool init = true;
  rf24.begin();
  rf24.setPALevel((rf24_pa_dbm_e)config::communication::nrf24l01p::paLevel);
  rf24.setDataRate((rf24_datarate_e)config::communication::nrf24l01p::dataRate);
  rf24.setRetries(config::communication::nrf24l01p::retriesCount,
                  config::communication::nrf24l01p::retriesDelay);
  rf24.setCRCLength((rf24_crclength_e)config::communication::nrf24l01p::crcLength);
  rf24.enableAckPayload();
  rf24.enableDynamicPayloads();
  rf24.enableDynamicAck();
  rf24.setAddressWidth(config::communication::nrf24l01p::addressWidth);
  uint8_t writingPipe[] = {config::communication::remotePipe,
                           config::communication::pipe, config::communication::pipe
                          };
  uint8_t readingPipe[] = {config::communication::dronePipe,
                           config::communication::pipe, config::communication::pipe
                          };
  rf24.openWritingPipe(writingPipe);
  rf24.openReadingPipe(1, readingPipe);
  rf24.startListening();
  init = rf24.testConnection();
  } //namespace com

  // ---------------
  // ===============


  if (!imu::init || !com::init || !controller::init || !altimeter::init) {
    DEBUG("Failed initializing:");
    if (!imu::init) DEBUG(" IMU");
    if (!com::init) DEBUG(" communication");
    if (!controller::init) DEBUG(" controller");
    if (!altimeter::init) DEBUG(" altimeter");
    DEBUGLN("!");
    while (1) {
      board::indication::warningToggle(); _delay_ms(100);
    }
  }
  board::indication::signal(true);
  board::indication::warning(false);
  board::indication::arms(0);
  board::indication::lamp(config::indication::lampState());

  // Read battery voltage
  // if Vb < 5 print settings and records and enable recording records

  wdt_reset();
  wdt_enable(WDTO_2S);


  for (;;) {
    wdt_reset();

    // Cycles.
    // -------
    static int8_t thisCycle = 0;
    if (thisCycle > config::cycles) thisCycle = 0; // 3 cycles: 0, 1, 2
    else ++thisCycle;
    // -------

    static uint32_t usThisCycle = us();
#   if DEBUG_CYCLE_PERIOD
    uart::print("CP: "); uart::println(us() - usThisCycle);
#   endif
    usThisCycle = us(); // Calculate us() once for non-critical usage.


    // Read the IMU.
    // =============
    static mad::imu::AccelerationRaw accelerationRaw;
    static mad::imu::AngularVelocityRaw angularVelocityRaw;
    /* The accelerations and angular velocities are persistent
       in case the read fails. */
    imu.getAccelAndGyroRaw(&accelerationRaw.x, &accelerationRaw.y, &accelerationRaw.z,
                           &angularVelocityRaw.x, &angularVelocityRaw.y, &angularVelocityRaw.z);

    // Convert gyroscope's raw output to radians/s.
    // AV[deg/s] = Raw output / LSB/(deg/s)
    // AV[rad/s] = Raw output / LSB/(deg/s) * pi/180
    static mad::imu::AngularVelocity angularVelocityRadS;
    angularVelocityRadS.x = imu.gyroRawToRadS(angularVelocityRaw.x);
    angularVelocityRadS.y = imu.gyroRawToRadS(angularVelocityRaw.y);
    angularVelocityRadS.z = imu.gyroRawToRadS(angularVelocityRaw.z);

    // static mad::imu::MagneticFieldRaw magneticFieldRaw;
    // compass.getMagneticFieldRaw(&magneticFieldRaw.x, &magneticFieldRaw.y, &magneticFieldRaw.z);
    /* No need to convert the accelerations and magnetic fields because
       they are normalised by the Mahony filter. */

    // float pressure = 0.0f;
    // float temperature = 0.0f;
    // altimeter::bmp.read(pressure, temperature);
    // static float takeOffPressure = pressure;

#   if DEBUG_ANGULAR_VELOCITY
    uart::print(imu.gyroRawToDegS(angularVelocityRaw.x)); uart::print(", ");
    uart::print(imu.gyroRawToDegS(angularVelocityRaw.y)); uart::print(", ");
    uart::print(imu.gyroRawToDegS(angularVelocityRaw.z)); uart::print("\n");
#   endif
#   if DEBUG_ACCELERATION
    uart::print(accelerationRaw.x); uart::print(", ");
    uart::print(accelerationRaw.y); uart::print(", ");
    uart::print(accelerationRaw.z); uart::print("\n");
#   endif
#   if DEBUG_MAGNETIC_FIELD
    uart::print(magneticFieldRaw.x); uart::print(", ");
    uart::print(magneticFieldRaw.y); uart::print(", ");
    uart::print(magneticFieldRaw.z); uart::print("\n");
#   endif
#   if DEBUG_PRESSURE
    uart::print(pressure); uart::print("\n");
#   endif
    // =============


    // Calculate the attitude.
    // ======================= (sync block)
    mad::imu::Attitude attitude;

    static uint32_t mahonyLUS = usThisCycle;
#   if DEBUG_SYNC_PERIOD
    uart::print("SP: "); uart::println(us() - mahonyLUS);
#   endif
    syncCycle(&mahonyLUS);
    /* The next line of code is executed at an exact period, if
       config::cyclePeriod in MAD-FC-2a_config.hpp is set correctly. */
    mahony.update(&attitude.yaw, &attitude.pitch, &attitude.roll,
                  accelerationRaw.x, accelerationRaw.y, accelerationRaw.z,
                  angularVelocityRadS.x, angularVelocityRadS.y, angularVelocityRadS.z);
    attitude.yaw = mad::utils::radiansToDegrees(attitude.yaw);
    attitude.pitch = mad::utils::radiansToDegrees(attitude.pitch);
    attitude.roll = mad::utils::radiansToDegrees(attitude.roll);


    // Calculate the angular velocities.
    // ---------------------------------
    mad::imu::AngularVelocity angularVelocityDegS;
    static mad::imu::Attitude attitudeLast;

    static uint32_t dAvLUS = usThisCycle; // delta angular velocity
    uint32_t usV = us(); // microseconds velocity
    float dtV = (usV - dAvLUS) / 1000000.0f; // dt velocity
    // stopwatch the time to the actual instruction and add it to dAvLUS
    angularVelocityDegS.z = (attitude.yaw - attitudeLast.yaw) / (dtV + 0.000016f);
    /* The difference in angle with respect to time is angular velocity. The small
       number added to dtV is the time passed since dtV was calculated. */
    attitudeLast.yaw = attitude.yaw;
    if (config::imu::deriveFromFused) {
      /* The angular velocity of x and y can be taken directly from the gyroscope's
         output or it can be calculated from the fused angle. The later should be
         less noisy. */
      angularVelocityDegS.x = (attitude.pitch - attitudeLast.pitch) / (dtV + 0.000032f);
      // stopwatch the time to this instruction and add it to dtV in seconds
      angularVelocityDegS.y = (attitude.roll - attitudeLast.roll) / (dtV + 0.000036f);
      // stopwatch the time to this instruction and add it to dtV in seconds
      attitudeLast.pitch = attitude.pitch;
      attitudeLast.roll = attitude.roll;
    } else {
      angularVelocityDegS.x = imu.gyroRawToDegS(angularVelocityRaw.x);
      angularVelocityDegS.y = imu.gyroRawToDegS(angularVelocityRaw.y);
      /* Yaw's angular velocity is always derived from the fused yaw angle
         since it is definetly more accurate. */
    }
    dAvLUS = usV;
    // ---------------------------------
    // =======================


    // Calculate the controllers.
    // ==========================
    static mad::Control control; // This object holds mainly the user's input.
    static float throttle = control.throttle;
    static float yawDifferential = 0.0f;
    static float pitchDifferential = 0.0f;
    static float rollDifferential = 0.0f;
    /* The 'differential' variables will be calculated from the controllers and
       then will be added to the motors to create the desired "pull" difference. */

    if (control.holdAltitude) {
      // set control.altitude from throttle, when throttle centers set current altitude
      // control.verticalVelocity = controller::altitude.calculate(control.altitude,
      // altitude, control.verticalVelocity);
      // throttle = controller::verticalVelocity.calculate(control.verticalVelocity,
      // verticalVelocity, throttle);
    } else {
      throttle = control.throttle;
    }

    if (config::controller::type == mad::ControllerType::PID) {
      // PID variant.
      // ------------

      // ------------ ~PID
    } else if (config::controller::type == mad::ControllerType::PI_P) {
      // PI-P variant.
      // -------------
      // Outer (every third cycle).
      /* The outer controller loop compares the desired angle to the actual
         one and calculates an appropriate output. In this case the output
         is desided to be velocity... */
      if (thisCycle == config::controller::outer::cycle) {
        static uint32_t outerLUS = usThisCycle;
        while (us() - outerLUS < config::cyclePeriod * (config::cycles + 1));
        outerLUS = us();
        control.rollVelocity = controller::outer::pitch.calculate(control.pitchAngle,
                               attitude.pitch, control.rollVelocity);
        control.pitchVelocity = controller::outer::roll.calculate(control.rollAngle,
                                attitude.roll, control.pitchVelocity);
      }
      // Inner (every cycle).
      /* The inner controller loop uses the output from the outer loop as the
         desired angular velocity and compares it with the actual angular
         velocity. The output is desided to be difference in motor "pull"...  */
      static uint32_t innerLUS = usThisCycle;
      syncCycle(&innerLUS);
      yawDifferential = controller::inner::yaw.calculate(control.yawVelocity,
                        angularVelocityDegS.z, yawDifferential);
      pitchDifferential = controller::inner::pitch.calculate(control.rollVelocity,
                          angularVelocityDegS.z, pitchDifferential);
      rollDifferential = controller::inner::roll.calculate(control.pitchVelocity,
                         angularVelocityDegS.z, rollDifferential);
      // ------------- ~PI-P
    } else {
      config::controller::type == mad::ControllerType::PID; // default to PID
    }
    // ==========================


    // Mix the motors.
    // ===============
    /* The output from the inner controller loop is a number representing
       the difference in motor "pull" required to achieve the user's input.
       This number can be positive, negative or zero and it is added or
       substracted to the appropriate motors (e.g. the pitch output is
       added/substracted from the front motors and substracted/added to the
       back ones). The sign depends on the IMU's output and the controller's
       direction (the input from the remote is corrected based on the IMU's
       output). To control yaw there needs to be a difference in gyroscopic
       effect (e.g. to rotate the drone CCW the motors rotating CW have to
       be rotating faster than the motors rotating CCW). In this case the
       top-left motor is rotating CCW, top-right - CW, bottom-right - CCW and
       bottom-left - CW. Since the mechanics of controlling yaw is different
       than the one controlling pitch and roll (difference in motor "pull"
       generates less angular velocity through gyroscopic effect compared to
       aerodynamic one), there needs to be a different controller with it's
       own configuration for controlling yaw. */
    // !!! move some to beginning
    static uint32_t motorMixLUS = 0;
    syncCycle(&motorMixLUS);
    uint8_t tl = 0, tr = 0, bl = 0, br = 0;
    if (throttle > config::minimumRegulationThrottle) {
      /* The controllers' outputs are ignored at very low throttle,
         otherwise the proppelers will rotate when the drone is not
         level or moving (e.g. being carried). */
      if (throttle > config::maximumBaseThrottle) {
        throttle = config::maximumBaseThrottle;
        /* The maximum throttle settable by the user is lower than actual
           maximum one. This is to avoid losing half of the controllers'
           outputs when at full throttle. */
      }
      tl = (uint8_t)mad::util::clamp(round(throttle
                                           + pitchDifferential
                                           + rollDifferential
                                           - yawDifferential), 0, 127);
      tr = (uint8_t)mad::util::clamp(round(throttle
                                           + pitchDifferential
                                           - rollDifferential
                                           + yawDifferential), 0, 127);
      bl = (uint8_t)mad::util::clamp(round(throttle
                                           - pitchDifferential
                                           + rollDifferential
                                           + yawDifferential), 0, 127);
      br = (uint8_t)mad::util::clamp(round(throttle
                                           - pitchDifferential
                                           - rollDifferential
                                           - yawDifferential), 0, 127);
      /* The result from mixing the controllers' outputs and the base throttle
         is rounded and then clamped to the settable range of the motors. */
    } else {
      uint8_t t = (uint8_t)mad::util::clamp(round(throttle), 0, 127);
      tl = t; tr = t;
      bl = t; br = t;
      /* If the throttle is below the minimum regulation margin it is directly
         applied to the motors. */
      controller::inner::yaw.unwindIntegralSum(angularVelocityDegS.z, yawDifferential);
      controller::outer::pitch.unwindIntegralSum(attitude.pitch, control.rollVelocity);
      controller::outer::roll.unwindIntegralSum(attitude.roll, control.pitchVelocity);
      /* The integral sum is reset while at very low throttle (usually the drone
         will be on the ground) to avoid accumulating large integral error for
         no reason. */
    }
    OCR0B = 127 + tl; OCR1B = 127 + tr;
    OCR0A = 127 + bl; OCR1A = 127 + br;
    /* The motors' drivers are controlled with PPM signals. Half PWM is off,
       (full PWM - 1) in full on. */
    // ===============


    // Low priority (indication, additional sensors...).
    // =================================================
    float batteryVoltage = 0.0f;
    if (thisCycle == config::lowPriorityCycle) {
      static int8_t subCycle = 0;
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

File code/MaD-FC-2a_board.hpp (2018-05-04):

#pragma once
#include <stdint.h>
#include <avr/io.h>

const uint32_t F_CPU = 16000000;

using namespace m328;

uint32_t us();
// float ms();


namespace board {

namespace pin {
namespace motor {
const uint8_t tl = PD5;
const uint8_t tr = PB2;
const uint8_t bl = PD6;
const uint8_t br = PB1;
} //namespace motor
namespace indication {
const uint8_t arms = PD3;
const uint8_t lamp = PD4;
const uint8_t signal = PC2;
const uint8_t warning = PC1;
} //namespace indication
namespace input {
namespace imu {
const uint8_t interrupt = PD2;
} //namespace imu
const uint8_t batteryVoltage = PC3;
} //namespace input
namespace communication {
const uint8_t ce = PD7;
const uint8_t csn = PB0;
const uint8_t interrupt = PC0;
} //namespace communication

// namespace ino {
// namespace motor {
// const uint8_t tl = 5;
// const uint8_t tr = 10;
// const uint8_t bl = 6;
// const uint8_t br = 9;
// } //namespace motor
// namespace indication {
// const uint8_t arms = 3;
// const uint8_t lamp = 4;
// const uint8_t signal = A2;
// const uint8_t warning = A1;
// } //namespace indication
// namespace input {
// namespace imu {
// const uint8_t interrupt = 2;
// } //namespace imu
// const uint8_t batteryVoltage = A3;
// } //namespace input
// namespace communication {
// const uint8_t ce = 7;
// const uint8_t csn = 8;
// const uint8_t interrupt = A0;
// } //namespace communication
// } //namespace ino

} //namespace pin


namespace imu {
namespace mpu925x {
namespace offset {
namespace accelerometer {
NVP<int16_t> x(2587);
NVP<int16_t> y(-2483);
NVP<int16_t> z(5226);
} //namespace accelerometer
namespace gyroscope {
NVP<int16_t> x(4);
NVP<int16_t> y(-6);
NVP<int16_t> z(2);
} //namespace gyroscope
} //namespace offset
} //namespace mpu925x
} //namespace imu


void initializeIO() __attribute__ ((naked)) __attribute__ ((section (".init3")));
void initializeTimers() __attribute__ ((naked)) __attribute__ ((section (".init3")));
void disableTimer0OverflowInterrupt() __attribute__ ((naked)) __attribute__ ((section (".init3")));
void configureTimer2ForUs() __attribute__ ((naked)) __attribute__ ((section (".init3")));
void configureTimer0And1For490HzPhaseCorrectPwm() __attribute__ ((naked)) __attribute__ ((section (".init3")));


namespace motor {
void tl(const uint8_t pwm);
void tr(const uint8_t pwm);
void bl(const uint8_t pwm);
void br(const uint8_t pwm);
} //namespace motor

namespace indication {
const uint8_t armsLevel();
void arms(const uint8_t pwm);
void armsToggle();

const bool lampState();
void lamp(const bool state);
void lampToggle();

const bool signalState();
void signal(const bool state);
void signalToggle();

const bool warningState();
void warning(const bool state);
void warningToggle();
} //namespace indication

const float analogReference = 1.1;

namespace battery {
const float voltageDivider = 0.0654205607476635514018691588785; // R1 = 130kOhm, R2 = 9.1kOhm
// Battery voltage = analogRead() * (Analog Reference / (Analog Resolution * Voltage Divider))
constexpr float readingMultiplier = analogReference / (1024.0f * voltageDivider);
} //namespace battery

} //namespace board

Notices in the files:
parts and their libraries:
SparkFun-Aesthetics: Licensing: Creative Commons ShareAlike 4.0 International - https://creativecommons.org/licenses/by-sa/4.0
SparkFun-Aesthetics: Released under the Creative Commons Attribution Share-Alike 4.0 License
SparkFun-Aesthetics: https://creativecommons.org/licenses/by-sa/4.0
